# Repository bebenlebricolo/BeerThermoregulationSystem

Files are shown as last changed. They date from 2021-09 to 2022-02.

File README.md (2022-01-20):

# Index
- [Index](#index)
- [BeerThermoregulationSystem](#beerthermoregulationsystem)
- [Subprojects/Components](#subprojectscomponents)
- [Power specs and power supply requirements](#power-specs-and-power-supply-requirements)
  - [Power supply minimum requirements](#power-supply-minimum-requirements)
- [Heat exchanger body](#heat-exchanger-body)

# BeerThermoregulationSystem

<div style="float:right;margin:0 0 0 0" markdown="1">
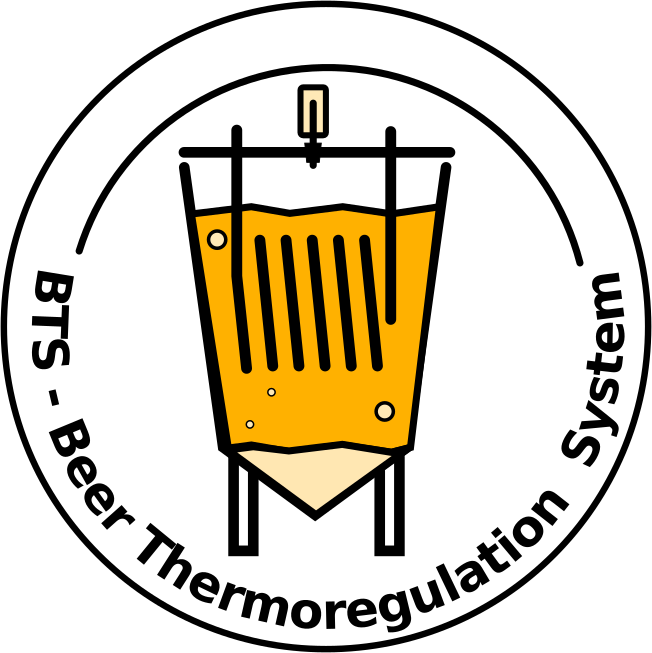
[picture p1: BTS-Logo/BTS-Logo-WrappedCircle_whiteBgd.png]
    
</div>

Beer thermoregulation system based on Peltier devices. Embeds mechanical design and electronic designs (as submodules)
This project aims to provide a complete electo-mechanical design whose role is to regulate fermenting beer temperature, using water-based heat exchanger.

# Subprojects/Components
It comes with 3 main hardware components (as opposed to 4 at the early days of the design) :
* Main heat exchanger body with 3D Cad design and 3D printed enclosures.
* [BTS-LogicBoard](https://github.com/bebenlebricolo/BTS-LogicBoard/blob/main/Readme.md) : electronic logic board whose role is to drive the power board with appropriate signals. It is full-featured and I designed it in a way that allows further improvements and extensions.
  * BTS-LogicBoard rev 0.3.0
* [BTS-MainBoard-Power](https://github.com/bebenlebricolo/BTS-MainBoard-Power/blob/main/Readme.md) : this electronic board drives the 8 Peltier modules used in this project and effectively acts as the main temperature regulation actuator. It was designed to work at relatively high frequencies (> 1MHz ) in order to reduce the overall board size and components price.
  * BTS-MainBoard-Power rev 0.2.0

# Power specs and power supply requirements
Each Peltier module (12v, 40x40 mm TEC12706, [manufacturer datasheet](https://docs.rs-online.com/aeb0/A700000007895121.pdf)) is able to draw 6.4Amps and move 57W each, which is the absolute maximum ratings for these devices ; in reality their efficiency is much lower, which explains the numbers !
The power board itself was designed to handle 40 Amps DC @ 12Volts (hence 480 W), in order to feed those 8 Peltier modules with around 5 Amps each, in both cooling and heating directions.

## Power supply minimum requirements
For my tests, I'm using a beefy PC ATX power supply (12V, 40Amps max) with around 600W capabilities.
These board setup is running it to its very limits and I think that's not a good idea on the long run.
So the PSU should be at least this powerful and able to deliver 40A+ steady DC current at 12V.

# Heat exchanger body
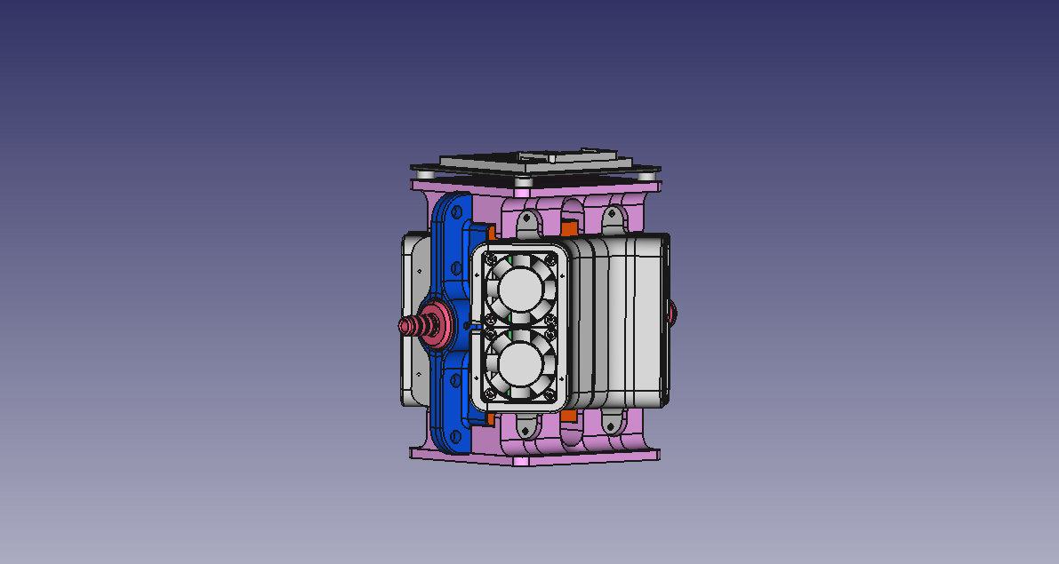
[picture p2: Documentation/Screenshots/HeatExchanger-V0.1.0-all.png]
heat exchanger

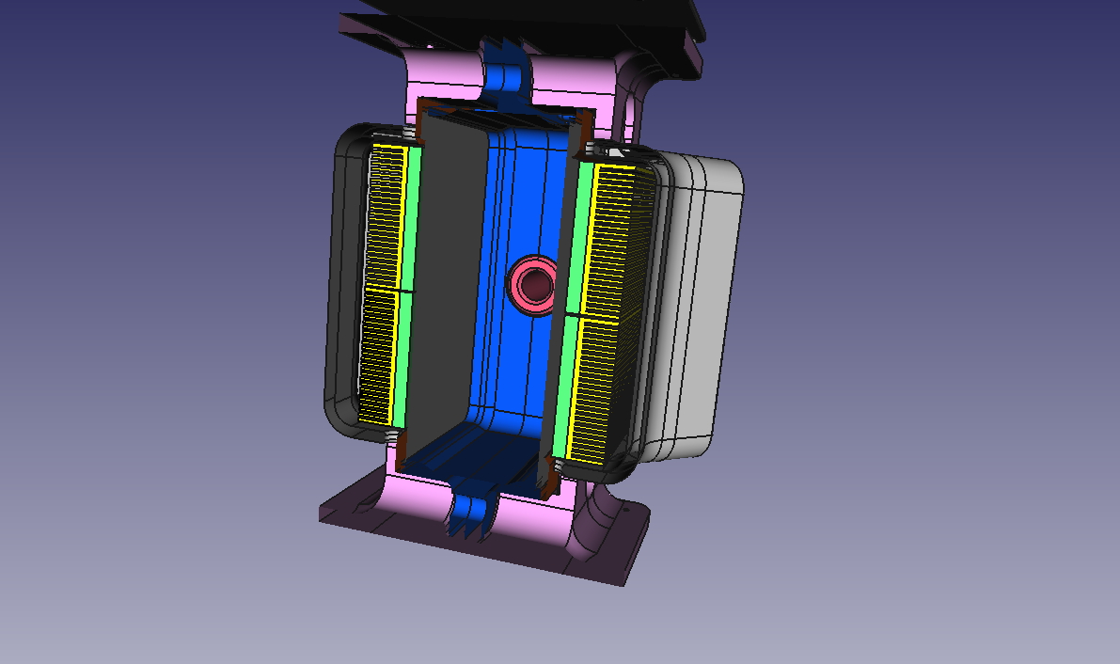
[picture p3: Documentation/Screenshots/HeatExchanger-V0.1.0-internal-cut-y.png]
heat exchanger internal cut


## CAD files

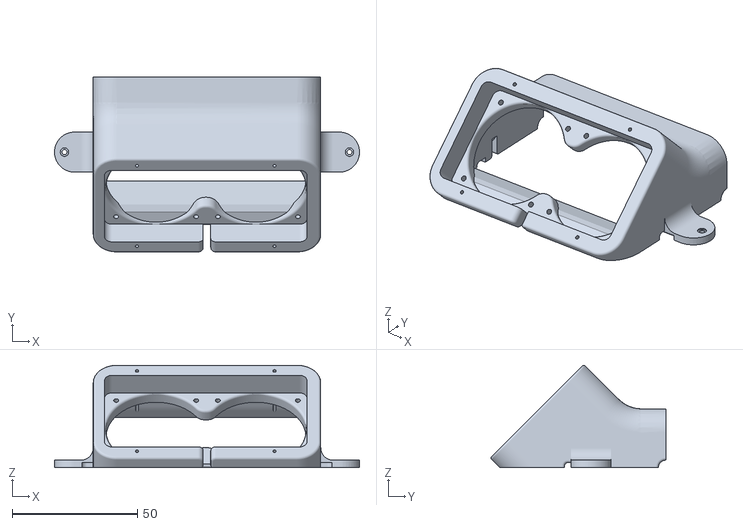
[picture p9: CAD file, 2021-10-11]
Mechanical/3DPrinting/AirDuct.stl
122.0 x 69.9 x 41.0

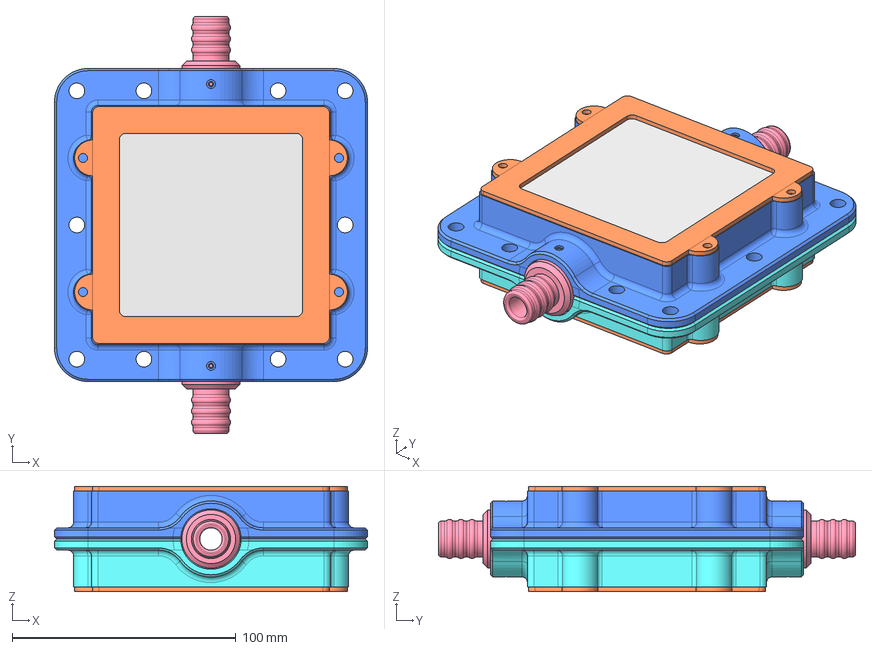
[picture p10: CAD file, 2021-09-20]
Mechanical/HeatExchangerCore.FCStd
140.0 x 186.5 x 47.0 mm
HalfCore1
HalfCore2
AluminumSheet
AluminumSheet2
CounterPlate
CounterPlate2
Inlet
Outlet

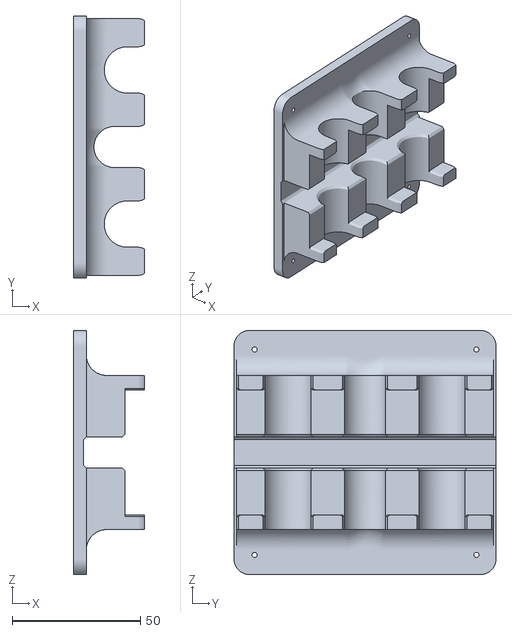
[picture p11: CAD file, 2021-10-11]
Mechanical/3DPrinting/BaseStand.stl
27.7 x 102.0 x 95.0

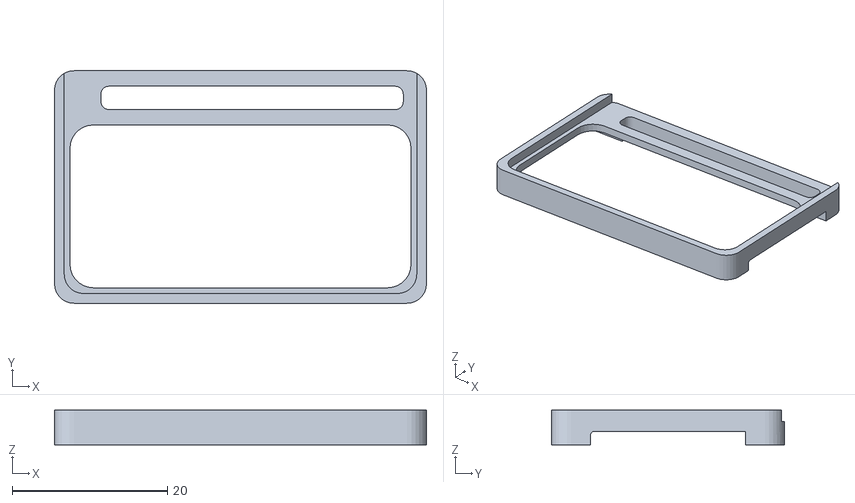
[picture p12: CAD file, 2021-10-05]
Mechanical/3DPrinting/MezzanineBoardHolder.stl
48.0 x 30.0 x 4.50

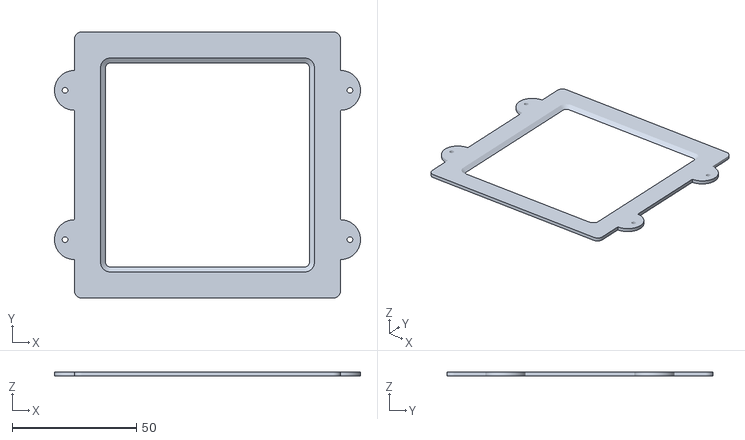
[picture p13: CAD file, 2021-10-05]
Mechanical/3DPrinting/CounterPlate.stl
123.0 x 107.0 x 1.75

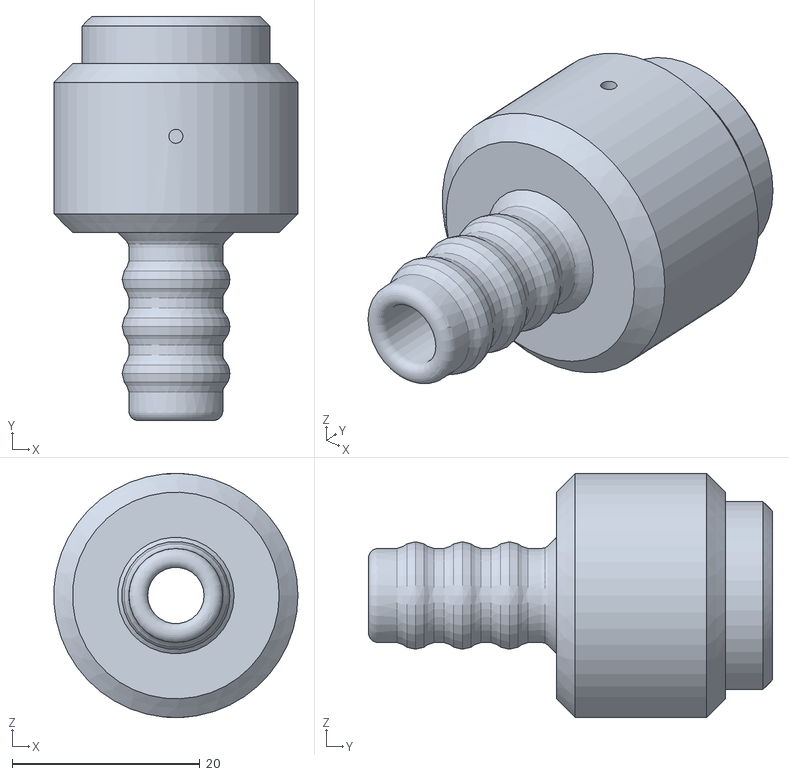
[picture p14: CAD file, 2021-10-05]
Mechanical/3DPrinting/SmallInlet.stl
26.0 x 43.0 x 26.0

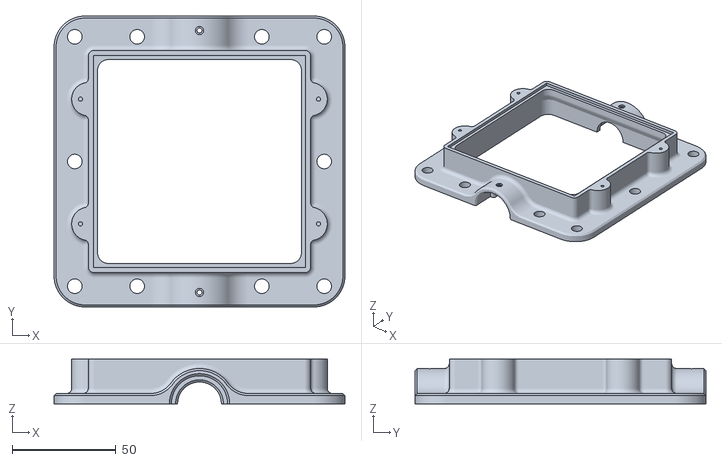
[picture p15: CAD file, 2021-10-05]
Mechanical/3DPrinting/HalfCore.stl
140.0 x 140.0 x 21.5

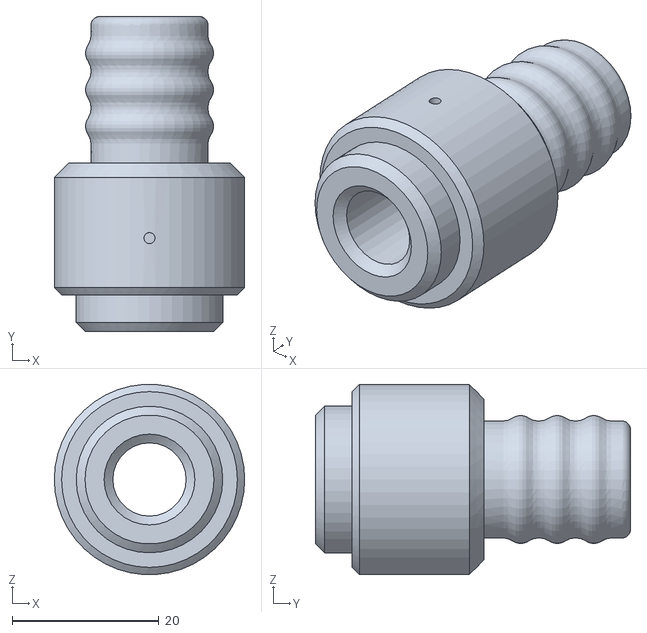
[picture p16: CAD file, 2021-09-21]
Mechanical/3DPrinting/LargeInlet.stl
26.0 x 43.0 x 26.0

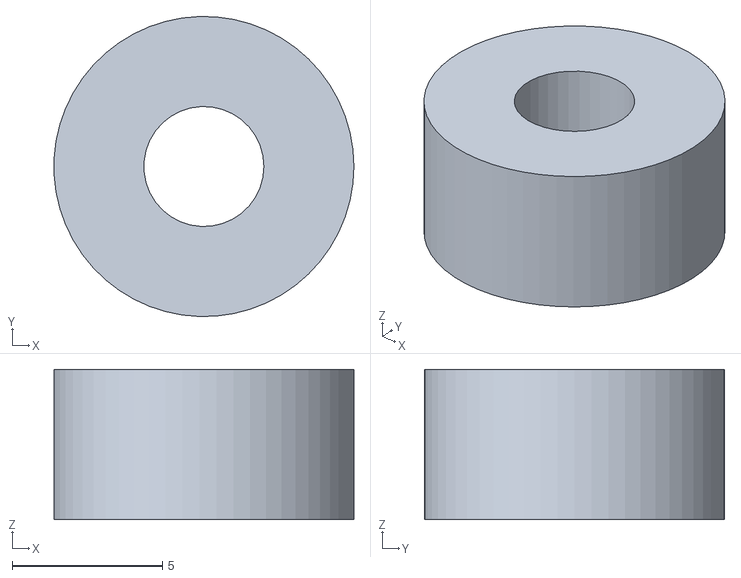
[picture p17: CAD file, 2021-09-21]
Mechanical/3DPrinting/Spacers.stl
9.99 x 10.00 x 5.00

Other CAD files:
Mechanical/3DPrinting/BoardHolder.stl

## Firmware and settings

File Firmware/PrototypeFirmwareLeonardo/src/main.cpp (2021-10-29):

#include <Arduino.h>
#include <string.h>
#include "maths.h"

// #########################################################################
// ########################## PIN mapping ##################################
// #########################################################################
// Input signals
#define DUTY_CYCLE_POT_PIN  (A0) // ADC7
#define POLARITY_SWITCH_PIN (11) // PB7
#define RESET_SWITCH_PIN    (12) // PD6

// Output signals
#define HIP_HEN_PWM_PIN     (13) // OC4A -> Fast PWM 10 bits timer (timer4) or atmega32u4
#define FAN_TRIGGER         (6)  // PD7
#define HIP_DIS_PIN         (7)  // PE6
#define IN_POS_PIN          (8)  // PB4
#define IN_NEG_PIN          (9)  // PB5

// #########################################################################
// ########################## Pot constants ################################
// #########################################################################

#define POT_LOW_THRESHOLD (200U)    // When pot signal goes under this threshold, output PWM is set to low state
#define POT_HIGH_THRESHOLD (800U)   // When pot signal goes above this threshold, output PWM is always set to high state
#define TIMER4_TOP_VALUE (15U)      // PWM will span from 0 - 63 with a prescaler of 1 ; generating a PWM frequency of 1MHz with 16 th steps (0 = 0%, 15 = 100%)
#define POT_MAPPED_RANGE_MAX (TIMER4_TOP_VALUE)   // POT is mapped between 0 and 63


// Potentiometer mapping constants
static constexpr map_ranges_t POT_INPUT_RANGE = {.start = POT_LOW_THRESHOLD, .end = POT_HIGH_THRESHOLD};
static constexpr uint16_t POT_INPUT_RANGE_SPAN = (POT_HIGH_THRESHOLD - POT_LOW_THRESHOLD);
static constexpr map_ranges_t POT_OUTPUT_RANGE = {.start = 0, .end = POT_MAPPED_RANGE_MAX};  // Output range is directly expressed as TIMER4 output compare value (OCR4A)
static constexpr uint16_t POT_OUTPUT_RANGE_SPAN = POT_MAPPED_RANGE_MAX;

// Minimum potentiometer value difference threshold used to
// detect a new "potentiometer event".
// As we don't want to update the output PWM constantly, we need to implement a small hysteresis
static constexpr uint16_t POT_MIN_DIFF_THRESHOLD = 20U; // Threshold expressed in the output pot range (matches TIMER4 OCR4A value)
static uint16_t last_pot_value = 0; /**< Last mapped potentiometer value, 0 to OCR4A */

// #########################################################################
// ########################## Static functions #############################
// #########################################################################

/**
 * @brief maps the potentiometer value from 0% to 100% within the evaluated range
 * Pot value has to be within the range defined by both POT high and low values
*/
static inline uint16_t map_pot(uint16_t potval);
static inline void stop_timer4(void);
static inline void start_timer4(void);
static inline uint16_t abs_difference(uint16_t const * const val1, uint16_t const * const val2 );

void setup() {
  //Serial.begin(9600);

  // put your setup code here, to run once:
  pinMode(DUTY_CYCLE_POT_PIN, INPUT);

  // Reset pin will take down all outputs at once
  pinMode(RESET_SWITCH_PIN, INPUT_PULLUP);
  pinMode(POLARITY_SWITCH_PIN, INPUT_PULLUP);

  // Output pins
  pinMode(HIP_HEN_PWM_PIN, OUTPUT);  // OC4A -> Will generate a PWM which goes to HEN pin of HIP4080A driver
  //DDRC |= (1 << PC7);
  //PORTC &= ~(1 << PC7); // No pullup on PC7
  pinMode(HIP_DIS_PIN, OUTPUT);      // PE6 -> Actively disables the HUP4080a driver (disables at "high" state)
  pinMode(FAN_TRIGGER, OUTPUT);      // PD7 -> Controls power board cooling fans
  pinMode(IN_POS_PIN, OUTPUT);       // PB4 -> Used as IN+ port of HIP4080A driver
  pinMode(IN_NEG_PIN, OUTPUT);       // PB5 -> Used as IN- port of HIP4080A driver

  // Default values for output ports ; disables everything before starting
  digitalWrite(HIP_DIS_PIN, 1U);
  digitalWrite(FAN_TRIGGER, 0U);
  digitalWrite(IN_POS_PIN, 0U);
  digitalWrite(IN_NEG_PIN, 0U);

  //Serial.println("Configuring timer 4");

  // Setup Timer4 with PLL and
  TCCR4A = (1 << COM4A1) | (1 << PWM4A); // COM4A1 set : OC4A pin connected (Cleared on compare match)
  TCCR4B = (1 << CS40); // Prescaler is equal to 1 ; timer will go at full speed
  TCCR4D = 0;
  //TCCR4D &= ~((1 << WGM41) | (1 << WGM40)); // Fast PWM mode
  TCNT4 = 0;
  TC4H = 0;
  OCR4A = 0;   // Output compare is set to 0, so that output is always low even if timer is running
  OCR4C = TIMER4_TOP_VALUE; // Gives a PWM at 1MHz with 16 resolution steps for timer4
}

void loop() {
  // put your main code here, to run repeatedly:
  uint16_t pot = (uint16_t) analogRead(DUTY_CYCLE_POT_PIN);

  bool rst_switch_on = (bool) digitalRead(RESET_SWITCH_PIN);
  bool pol_switch_on = (bool) digitalRead(POLARITY_SWITCH_PIN);

  // Check if a reset is ongoing
  if (!rst_switch_on)
  {
    digitalWrite(FAN_TRIGGER, 1U);  // Activate cooling fans all at once

    // Check polarity to know if we are cooling or heating
    if (pol_switch_on)
    {
      digitalWrite(IN_POS_PIN, 1U);
      digitalWrite(IN_NEG_PIN, 0U);
    }
    else
    {
      digitalWrite(IN_POS_PIN, 0U);
      digitalWrite(IN_NEG_PIN, 1U);
    }

    // Handle PWM setup
    if (pot < POT_LOW_THRESHOLD)
    {
      stop_timer4();
      //Serial.println("POT val too small");
      digitalWrite(HIP_HEN_PWM_PIN, LOW); // Disables HIP4080a driver
      digitalWrite(HIP_DIS_PIN, 1U);
    }
    else if (pot > POT_HIGH_THRESHOLD)
    {
      //Serial.println("POT val too big");
      stop_timer4();
      digitalWrite(HIP_DIS_PIN, 0U);
      digitalWrite(HIP_HEN_PWM_PIN, HIGH); // overrides PWM
    }
    else
    {
      uint16_t mapped_pot_value = map_pot(uint16_t(pot));
      // Only update timer's output frequency if potentiometer reading varied in a meaningfull way
      if (abs_difference(&last_pot_value, &pot) >= POT_MIN_DIFF_THRESHOLD)
      {
        last_pot_value = mapped_pot_value;
        // sprintf(msg, "Map val : %d", mapped_pot_value);
        // Serial.println(msg);
        // sprintf(msg, "Real val : %d", pot);
        // Serial.println(msg);
        // Program Timer4 to generate PWM with the right frequency
        start_timer4(); // no effect is timer is already started
        OCR4A = (uint8_t) mapped_pot_value;
        digitalWrite(HIP_DIS_PIN, 0U);
      }
    }

  }
  else  // Reset switch is activated ( disabling everything )
  {
    // Disable both outputs
    digitalWrite(IN_POS_PIN, 0U);
    digitalWrite(IN_NEG_PIN, 0U);
    digitalWrite(FAN_TRIGGER, 0U);  // Activate cooling fans all at once

    // Actively disables HIP driver
    digitalWrite(HIP_DIS_PIN, 1U);
    digitalWrite(HIP_HEN_PWM_PIN, 0U); // Disables HIP4080a driver
    stop_timer4();
  }
}

/**
 * @brief maps the potentiometer value from 0% to 100% within the evaluated range
 * Pot value has to be within the range defined by both POT high and low values
*/
static inline uint16_t map_pot(uint16_t potval)
{
  uint16_t mapped = linear_remap(potval, &POT_INPUT_RANGE, &POT_OUTPUT_RANGE);
  return mapped;
}

static inline void stop_timer4(void)
{
  TCCR4B &= 0xF0; // CSxx bits
}

static inline void start_timer4(void)
{
  TCCR4B |= (1 << CS40); // Re-enables timer 4 PWM on pin A
  TCCR4A = (1 << COM4A1) | (1 << PWM4A);
}

static inline uint16_t abs_difference(uint16_t const * const val1, uint16_t const * const val2 )
{
  uint16_t out = 0;
  if( *val1 > *val2)
  {
    out = *val1 - *val2;
  }
  else
  {
    out = *val2 - *val1;
  }
  return out;
}

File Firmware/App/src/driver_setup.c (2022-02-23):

/*

------------------
@<FreeMyCode>
FreeMyCode version : 1.0 RC alpha
    Author : bebenlebricolo
    License :
        name : GPLv3
        url : https://www.gnu.org/licenses/quick-guide-gplv3.html
    Date : 12/02/2021
    Project : LabBenchPowerSupply
    Description : The Lab Bench Power Supply provides a simple design based around an Arduino Nano board to convert AC main voltage into
 smaller ones, ranging from 0V to 16V, with voltage and current regulations
<FreeMyCode>@
------------------

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
You should have received a copy of the GNU General Public License
along with this program.  If not, see <https://www.gnu.org/licenses/>.
*/

#include "driver_setup.h"

#include <avr/io.h>
#include "adc.h"
#include "timer_8_bit.h"
#include "timer_8_bit_async.h"
#include "timer_16_bit.h"
#include "i2c.h"
#include "HD44780_lcd.h"

#include "pin_mapping.h"
driver_setup_error_t driver_init_adc(void)
{
    adc_config_hal_t config;
    adc_config_hal_get_default(&config);
    config.prescaler = ADC_PRESCALER_64;
    config.ref = ADC_VOLTAGE_REF_AVCC;
    config.running_mode = ADC_RUNNING_MODE_SINGLE_SHOT;
    config.supply_voltage_mv = 5000;
    config.using_interrupt = true;


    adc_error_t init_err = adc_base_init(&config);
    if (ADC_ERROR_OK != init_err)
    {
        return DRIVER_SETUP_ERROR_INIT_FAILED;
    }
    return DRIVER_SETUP_ERROR_OK;
}


driver_setup_error_t driver_init_timer_0(void)
{
    timer_8_bit_config_t config;
    timer_error_t local_error;
    {
        local_error = timer_8_bit_get_default_config(&config);
        if (TIMER_ERROR_OK != local_error)
        {
            return DRIVER_SETUP_ERROR_INIT_FAILED;
        }
    }

    /* Configuring handle */
    config.handle.OCRA = &OCR0A;
    config.handle.OCRB = &OCR0B;
    config.handle.TCCRA = &TCCR0A;
    config.handle.TCCRB = &TCCR0B;
    config.handle.TCNT = &TCNT0;
    config.handle.TIFR = &TIFR0;
    config.handle.TIMSK = &TIMSK0;

	/* Enable OC0A and OC0B as outputs */
    OC0A_DDR_REG |= (1 << OC0A_PIN_NUMBER);
    OC0B_DDR_REG |= (1 << OC0B_PIN_NUMBER);

    /* Set original port state of OC0A/OC0B pins before any OCRx overrides them */
    /* This is done in opposing polarities to respect mosfet push-pull driver pair starting point*/
    OC0A_PORT_REG |= (1 << OC0A_PIN_NUMBER);
    OC0B_PORT_REG &= ~(1 << OC0B_PIN_NUMBER);

    /* Configuring timer */
    /* F_CPU = 16'000'000 Hz ; F_TIMER0 2'000'000 Hz*/
    /* 8-bit wide -> 256 values => F_PWM_0 = 7812 Hz*/
    config.timing_config.prescaler = TIMER8BIT_CLK_PRESCALER_8;
    config.timing_config.waveform_mode = TIMER8BIT_WG_PWM_FAST_FULL_RANGE;
    /* Invert OC0x behavior to provide a correct PWM for a push-pull driver pair */
    config.timing_config.comp_match_a = TIMER8BIT_CMOD_CLEAR_OCnX;
    config.timing_config.comp_match_b = TIMER8BIT_CMOD_SET_OCnX;
    /* Duty cycle : 39 % */
    config.timing_config.ocra_val = 99;
    config.timing_config.ocrb_val = 99;

    {
        local_error = timer_8_bit_init(0, &config);
        if (TIMER_ERROR_OK != local_error)
        {
            return DRIVER_SETUP_ERROR_INIT_FAILED;
        }
    }
    return DRIVER_SETUP_ERROR_OK;
}

driver_setup_error_t driver_init_timer_1(void)
{
    timer_16_bit_config_t config;
    timer_error_t local_error;
    {
        local_error = timer_16_bit_get_default_config(&config);
        if (TIMER_ERROR_OK != local_error)
        {
            return DRIVER_SETUP_ERROR_INIT_FAILED;
        }
    }

    /* Configuring handle */
    config.handle.OCRA_H = &OCR1AH;
    config.handle.OCRA_L = &OCR1AL;
    config.handle.OCRB_H = &OCR1BH;
    config.handle.OCRB_L = &OCR1BL;
    config.handle.TCCRA = &TCCR1A;
    config.handle.TCCRB = &TCCR1B;
    config.handle.TCCRC = &TCCR1C;
    config.handle.TCNT_H = &TCNT1H;
    config.handle.TCNT_L = &TCNT1L;
    config.handle.TIFR = &TIFR1;
    config.handle.TIMSK = &TIMSK1;
    config.handle.ICR_H = &ICR1H;
    config.handle.ICR_L = &ICR1L;

	/* Enable OC0A and OC0B as outputs */
    /* PD6 = OC0A on arduino nano */
    /* PD5 = OC0B on arduino nano */
    OC1A_DDR_REG |= (1 << OC1A_PIN_NUMBER);
    OC1B_DDR_REG |= (1 << OC1B_PIN_NUMBER);

    /* Set original port state of OC0A/OC0B pins before any OCRx overrides them */
    /* This is done in opposing polarities to respect mosfet push-pull driver pair starting point*/
    OC1A_PORT_REG |= (1 << OC1A_PIN_NUMBER);    // Pulled to Vcc (low side of mosfet driver pulls mosfet's gate to ground)
    OC1B_PORT_REG &= ~(1 << OC1B_PIN_NUMBER);   // Pulled to ground (high side of mosfet driver is depleted)

    /* Configuring timer */
    /* F_CPU = 16'000'000 Hz ; F_TIMER0 2'000'000 Hz*/
    /* 10-bit wide -> 1024 values => F_PWM_1 = 1953 Hz*/
    config.timing_config.prescaler = TIMER16BIT_CLK_PRESCALER_8;
    config.timing_config.waveform_mode = TIMER16BIT_WG_PWM_FAST_10_bit_FULL_RANGE;
    /* Invert OC0x behavior to provide a correct PWM for a push-pull driver pair */
    config.timing_config.comp_match_a = TIMER16BIT_CMOD_CLEAR_OCnX;
    config.timing_config.comp_match_b = TIMER16BIT_CMOD_SET_OCnX;
    /* Duty cycle : 50 % */
    config.timing_config.ocra_val = 512;
    config.timing_config.ocrb_val = 512;

    {
        local_error = timer_16_bit_init(0, &config);
        if (TIMER_ERROR_OK != local_error)
        {
            return DRIVER_SETUP_ERROR_INIT_FAILED;
        }
    }
    return DRIVER_SETUP_ERROR_OK;
}
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

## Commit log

2021-09-20 Started Mechanical design in FreeCad
    [HeatExchangerCore.FCStd]
2021-09-20 Added peltiers, heatsinks and fans to design
2021-09-20 Moved Power board mockup to the sides
2021-09-20 Almost finalized heat exchanger
2021-09-21 Exported STL files for 3D printing
    [HeatExchangerCore-BTS-MainPower-Power-MockupBlock.stl, HeatExchangerCore-BTS-MainPower-Power-MockupBoardHolder.stl, HeatExchangerCore-BaseStand.stl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]
2021-09-21 Added chamfer to HalfCore piece and exported stl
    [HeatExchangerCore-CoreExchangerHalfCore1.stl]
2021-09-22 Added Air duct to exports
    [HeatExchangerCore-AirDuct.stl]
2021-09-23 Updated Base stand stl
    [HeatExchangerCore-BaseStand.stl]
2021-10-05 Updated inlets with small diameter as well
    [SmallInlet.stl]
2021-10-05 Updated half core part and counter plate + reexported all
    [AirDuct.stl, BaseStand.stl, BoardHolder.stl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]
2021-10-05 Updated Half core and counter plate + reexported files
    [CounterPlate.stl, HalfCore.stl]
2021-10-05 Modified AirDuct with a channel for fans wires + mezzanine board
    [AirDuct.stl, CounterPlate.stl, MezzanineBoardHolder.stl]
2021-10-05 Cleaned boards history
2021-10-06 Updated submodules and moved BOMS out of kicad folders
2021-10-08 Updated AirDuct with proper holes for Peltier module's wires
    [AirDuct.stl]
2021-10-11 Updated mechanical design and BTS-LogicBoard (V1.1)
    [AirDuct.stl, BaseStand.stl, BoardHolder.stl]
2021-10-19 Synchronized with boards
2021-10-20 Updated boards submodules
2021-10-22 Started temp implementation with arduino leonardo
2021-10-23 Updated arduino firmware
2021-10-23 Working firmware (update with arduino IDE instead of platformio\!)
2021-10-29 Fixed wrong HIP Pin disable behavior
    [main.cpp]
2022-01-20 Updated BTS-LogicBoard with Avr MCU hardware and Power board with new arch
2022-01-24 Synced up with latest changes on boards
2022-02-23 Archived old prototype firmware and copied code from LabBenchPowerSupply
